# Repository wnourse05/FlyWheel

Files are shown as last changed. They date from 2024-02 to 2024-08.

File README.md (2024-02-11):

# FlyWheel

Hardware and Software for FlyWheel, a mobile robot for testing models of Fruit Fly Vision.

## Project Organization
- /hardware: Bill of materials and stl files for manufacturing FlyWheel
- /sns_flywheel: ROS package for controlling FlyWheel
- camera_overrides.isp: Preference file for proper color calibration of the cameras, from https://jonathantse.medium.com/fix-pink-tint-on-jetson-nano-wide-angle-camera-a8ce5fbd797f. See Installation for details
- robot_driver.ino: Arduino sketch to control the motors as a ros node.

## Installation

### Hardware Configuration
Please refer to the hardware directory for more information.

### Software Configuration
- Flash the sd card and set up the Jetson following the directions at: https://developer.nvidia.com/embedded/learn/get-started-jetson-orin-nano-devkit#intro . This project is built using Jetpack 5.1.2, available at: https://developer.nvidia.com/embedded/jetpack-sdk-512
- Install ROS-Noetic following the instructions at: http://wiki.ros.org/noetic
- Set up a catkin workspace following the instructions at: http://wiki.ros.org/ROS/Tutorials/InstallingandConfiguringROSEnvironment
- Clone this repository into ~/catkin_ws/src
- Install the joy package using "sudo apt-get install ros-noetic-joy"
- Install pip: sudo apt install python3-pip
- Install libopenblas: sudo apt-get install libopenblas-dev
- Upgrade numpy: pip install --upgrade numpy
- Export the NVIDIA Jetson torch url using: export TORCH_INSTALL=https://developer.download.nvidia.cn/compute/redist/jp/v511/pytorch/torch-2.0.0+nv23.05-cp38-cp38-linux_aarch64.whl
- Install torch: pip install --no-cache $TORCH_INSTALL 
- Correct the camera color profiles using camera_overrides.isp, following the directions at https://jonathantse.medium.com/fix-pink-tint-on-jetson-nano-wide-angle-camera-a8ce5fbd797f

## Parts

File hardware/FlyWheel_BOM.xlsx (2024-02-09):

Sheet: Overall BOM
Name | Description | Unit Cost | Quantity | Extended Cost | Source
Robot Base
M2 Male to Male Nylon Hex Standoff Plastic Thread Motherboard Spacer Prototyping Accessories for PCB, Quadcopter Drone, Computer & Circuit Board Assortment Kit Black | Standoffs | $14.88 | 1 | $14.88 | https://www.amazon.com/gp/product/B07D78PFQL/ref=ppx_yo_dt_b_asin_title_o05_s00?ie=UTF8&psc=1
TB3 Wheel Tire Set-ISW-01 (2ea) | Dynamixel Wheels | $9.40 | 1 | $9.40 | https://www.robotis.us/tb3-wheel-tire-set-isw-01-2ea/
DYNAMIXEL XL430-W250-T | Motor | $49.90 | 2 | $99.80 | https://www.robotis.us/dynamixel-xl430-w250-t/
Cable Zip Ties,400 Pack Black Assorted Sizes 12+8+6+4 Inch,Multi-Purpose Self-Locking Nylon Cable Cord Management ,Plastic Wire Ties for Home,Office,Garden,Workshop. By HAVE ME TD | Zip Ties | $5.99 | 1 | $5.99 | https://www.amazon.com/HAVE-ME-TD-Cable-Ties/dp/B08TVLYB3Q
OpenRB-150 | Serial controller | $24.90 | 1 | $24.90 | https://www.robotis.us/openrb-150/
Robot Cable-3P 100mm 10pcs | Cables | $14.20 | 1 | $14.20 | https://www.robotis.us/robot-cable-3p-100mm-10pcs/
FP04-F18 2pcs | Dynamixel Tires | $3.80 | 1 | $3.80 | https://www.robotis.us/fp04-f18-2pcs/
Ball Caster - 3/4" Metal Ball | Roller ball | $4.95 | 1 | $4.95 | https://www.adafruit.com/product/1200
ELEGOO PLA Filament 1.75mm Black | Filament | $13.99 | 1 | $13.99 | https://www.amazon.com/gp/product/B0BM739JRF/ref=ppx_yo_dt_b_asin_title_o05_s00?ie=UTF8&psc=1
JXMOX Short USB C to USB C Cable 60W, (2 Pack 1ft) Type C Fast Charging Cord Charger Compatible with iPhone 15 Plus/15 Pro Max, MacBook Pro, iPad Pro Air 4, Samsung Galaxy S23+ S22 S21 Ultra (Grey) | USB C to C Cable | $5.68 | 1 | $5.68 | https://www.amazon.com/gp/product/B07TVMBZ75/ref=ppx_yo_dt_b_asin_title_o05_s00?ie=UTF8&th=1
Talentcell Lithium ion Battery Pack NB7102, Rechargeable 17500mAh 64.75Wh Li-ion Power Bank with DC 24/19/5V and USB-C 5/9/12/15/20V Output for Laptop, Notebook, Smartphone, Camera and More | Battery | $62.99 | 1 | $62.99 | https://www.amazon.com/gp/product/B07RDFM55J/ref=ppx_od_dt_b_asin_title_s00?ie=UTF8&psc=1
3FT 12V DC Power Cable | 5.5mm x 2.1mm Male Plug to Bare Wire Open End | 16AWG 24V DC Power Supply Repair Cable | for CCTV Security Camera LED Strip Light | Motor power cable | $5.99 | 1 | $5.99 | https://www.amazon.com/gp/product/B09SQCY6BC/ref=ppx_od_dt_b_asin_title_s00?ie=UTF8&psc=1
Valefod 3 Pack LM2596 DC to DC Voltage Regulator | 4-40V to 1.5-35V Buck Converter | with LED Display | Buck Regulator | $13.99 | 1 | $13.99 | https://www.amazon.com/gp/product/B07WQJ2GD6/ref=ppx_od_dt_b_asin_title_s02?ie=UTF8&psc=1
Arduino MKR IMU Shield [ASX00002] Original Arduino Board Made in Italy Based on BNO055 Absolute Orientation Sensor 14-bit Accelerometer a triaxial 16-bit Gyroscope triaxial geomagnetic Sensor | IMU | $29.99 | 1 | $29.99 | https://www.amazon.com/gp/product/B09RPBKSZT/ref=ppx_od_dt_b_asin_title_s03?ie=UTF8&psc=1
 |  |  | Subtotal: | $310.55
Robot Computation
Yahboom 8MP IMX219 CSI Camera Compatible with NVIDIA Jetson Nano Developer Kit 3280×2464 Vision IR 77°/120°/160° Ultra Wide Angle Camera Module (IMX219 160°Camera+15/22pin) | 160 degree CSI camera | $28.99 | 2 | $57.98 | https://www.amazon.com/gp/product/B0C584LT6F/ref=ox_sc_act_title_1?smid=A1N1A77RUX51FT&psc=1
Arcade Button with LED - 30mm Translucent Clear | Power button | $2.50 | 1 | $2.50 | https://www.adafruit.com/product/3491
GL.iNet GL-SFT1200 (Opal) Secure Travel WiFi Router – AC1200 Dual Band Gigabit Ethernet Wireless Internet Router | IPv6 | USB 2.0 | MU-MIMO | DDR3 |128MB Ram | Repeater Bridge | Access Point Mode | Router | $39.90 | 1 | $39.90 | https://www.amazon.com/GL-iNet-GL-SFT1200-Secure-Travel-Router/dp/B09N72FMH5
Cat 8 Ethernet Cable, 1.5Ft 3Ft 6Ft 10Ft 15Ft 20Ft 30Ft 40Ft 50Ft 60Ft 100Ft Heavy Duty High Speed Internet Network Cable, Professional LAN Cable Shielded in Wall, Indoor&Outdoor | Ethernet | $2.99 | 1 | $2.99 | https://www.amazon.com/dp/B08PL53JG3/ref=twister_B08PP81V1L?_encoding=UTF8&psc=1
NVIDIA Jetson Orin Nano Developer Kit | Computer | $499.00 | 1 | $499.00 | https://www.amazon.com/NVIDIA-Jetson-Orin-Nano-Developer/dp/B0BZJTQ5YP
ELEGOO 120pcs Multicolored Dupont Wire 40pin Male to Female, 40pin Male to Male, 40pin Female to Female Breadboard Jumper Ribbon Cables Kit Compatible with Arduino Projects | Button wires | $6.98 | 1 | $6.98 | https://www.amazon.com/Elegoo-EL-CP-004-Multicolored-Breadboard-arduino/dp/B01EV70C78
GameSir T3s Wireless Gaming Controller for Switch, PC Windows, Bluetooth Controller with Turbo Function, Dual Shock, 25 Hours of Playing Time for Android/iPhone/Android TV Box/Tablet (Black) | Controller | $30.99 | 1 | $30.99 | https://www.amazon.com/gp/product/B09ZQWR5RD/ref=ppx_od_dt_b_asin_title_s01?ie=UTF8&th=1
SanDisk 128GB Extreme microSDXC UHS-I Memory Card with Adapter | Up to 190MB/s | C10 | U3 | V30 | 4K | 5K | A2 | Micro SD Card | SDSQXAA-128G-GN6MA | uSD card | $19.99 | 1 | $19.99 | https://www.amazon.com/gp/product/B09X7BK27V/ref=ppx_od_dt_b_asin_title_s02?ie=UTF8&th=1
Arcade Button Quick-Connect Wire Pairs - 0.11" (10 pack) | Button wires | $4.95 | 1 | $4.95 | https://www.adafruit.com/product/1152
Jumper Shunt with Handle (0.1" / 2.54mm) – 10 Pack | Shunt | $0.95 | 1 | $0.95 | https://www.adafruit.com/product/3525
 |  |  | Subtotal: | $666.23
 |  |  | Total: | $976.78

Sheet: Adafruit
Name | Description | Unit Cost | Quantity | Extended Cost | Source
Ball Caster - 3/4" Metal Ball | Roller ball | $4.95 | 1 | $4.95 | https://www.adafruit.com/product/1200
Adafruit TDK InvenSense ICM-20948 9-DoF IMU (MPU-9250 Upgrade) - STEMMA QT / Qwiic | IMU | $14.95 | 1 | $14.95 | https://www.adafruit.com/product/4554
STEMMA QT / Qwiic JST SH 4-pin Cable with Premium Female Sockets - 150mm Long | IMU cable | $0.95 | 1 | $0.95 | https://www.adafruit.com/product/4397
Arcade Button with LED - 30mm Translucent Clear | Power button | $2.50 | 1 | $2.50 | https://www.adafruit.com/product/3491
 |  |  | Total: | $23.35

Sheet: Robotis
Name | Description | Unit Cost | Quantity | Extended Cost | Source
FP04-F17 2pcs | Dynamixel Wheels | $2.50 | 1 | $2.50 | https://www.robotis.us/fp04-f17-2pcs/ | Robot base
DYNAMIXEL AX-12W | Motor | $49.90 | 2 | $99.80 | https://www.robotis.us/dynamixel-ax-12w/
U2D2 | Serial controller | $32.10 | 1 | $32.10 | https://www.robotis.us/u2d2/
Robot Cable-3P 100mm 10pcs | Cables | $14.20 | 1 | $14.20 | https://www.robotis.us/robot-cable-3p-100mm-10pcs/
FP04-F18 2pcs | Dynamixel Tires | $3.80 | 1 | $3.80 | https://www.robotis.us/fp04-f18-2pcs/
Robot Cable-X3P 180mm (Convertible) (10pcs) | Molex to JST Cable | $15.50 | 1 | $15.50 | https://www.robotis.us/robot-cable-x3p-180mm-convertible-10pcs/
U2D2 Power Hub Board Set | Power hub | $19.00 | 1 | $19.00 | https://www.robotis.us/u2d2-power-hub-board-set/
 |  |  | Total: | $186.90

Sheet: Amazon
Name | Description | Unit Cost | Quantity | Extended Cost | Source
M2 Male to Male Nylon Hex Standoff Plastic Thread Motherboard Spacer Prototyping Accessories for PCB, Quadcopter Drone, Computer & Circuit Board Assortment Kit Black | Standoffs | $8.99 | 1 | $8.99 | https://www.amazon.com/Motherboard-Prototyping-Accessories-Quadcopter-Assortment/dp/B07DBY4GQ8 | Robot Base
SUNGUY USB C Android Auto Cable 1FT, USB C to USB 3.1 USB 3.2 Gen2 10Gbps USB A to C Data Fast Charging Cable Compatible with Samsung Galaxy S21 S20 S10 S10E Note 20, USB C External C SSD, Pixel | USB A to C Cable | $7.99 | 1 | $7.99 | https://www.amazon.com/SUNGUY-Android-Charging-Compatible-External/dp/B0B28ZCV2Y | Robot Base
Talentcell Rechargeable 12V 6000mAh/5V 12000mAh DC Output Lithium ion Battery Pack for LED Strip and CCTV Camera, Portable Li-ion Power Bank with Charger, Black | Battery | $39.99 | 1 | $39.99 | https://www.amazon.com/TalentCell-Rechargeable-12000mAh-Multi-led-indicator/dp/B00ME3ZH7C | Robot Base
AILTECK 12V 5.5mm x 2.1mm Female to Female DC Power Connector Adapter, Male to Male Power Plug Jack Barrel for Led Strip Light CCTV Security Camera | Barrel adapter | $5.49 | 1 | $5.49 | https://www.amazon.com/AILTECK-Connector-Adapter-Female-Security/dp/B08V21NX8L | Robot Base
Yahboom 8MP IMX219 CSI Camera Compatible with NVIDIA Jetson Nano Developer Kit 3280×2464 Vision IR 77°/120°/160° Ultra Wide Angle Camera Module (IMX219 160°Camera+15/22pin) | 160 degree CSI camera | $28.99 | 2 | $57.98 | https://www.amazon.com/gp/product/B0C584LT6F/ref=ox_sc_act_title_1?smid=A1N1A77RUX51FT&psc=1 | Robot Compute
GL.iNet GL-SFT1200 (Opal) Secure Travel WiFi Router – AC1200 Dual Band Gigabit Ethernet Wireless Internet Router | IPv6 | USB 2.0 | MU-MIMO | DDR3 |128MB Ram | Repeater Bridge | Access Point Mode | Router | $39.90 | 1 | $39.90 | https://www.amazon.com/GL-iNet-GL-SFT1200-Secure-Travel-Router/dp/B09N72FMH5 | Robot Compute
Cat 8 Ethernet Cable, 1.5Ft 3Ft 6Ft 10Ft 15Ft 20Ft 30Ft 40Ft 50Ft 60Ft 100Ft Heavy Duty High Speed Internet Network Cable, Professional LAN Cable Shielded in Wall, Indoor&Outdoor | Ethernet | $2.99 | 1 | $2.99 | https://www.amazon.com/dp/B08PL53JG3/ref=twister_B08PP81V1L?_encoding=UTF8&psc=1 | Robot Compute
ELEGOO 120pcs Multicolored Dupont Wire 40pin Male to Female, 40pin Male to Male, 40pin Female to Female Breadboard Jumper Ribbon Cables Kit Compatible with Arduino Projects | Button wires | $6.98 | 1 | $6.98 | https://www.amazon.com/Elegoo-EL-CP-004-Multicolored-Breadboard-arduino/dp/B01EV70C78 | Robot Compute
 |  |  | Total: | $170.31

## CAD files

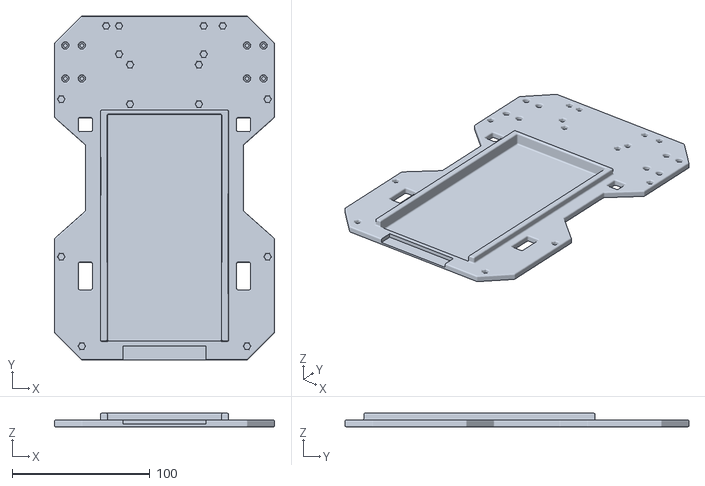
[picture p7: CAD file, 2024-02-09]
hardware/stl/base_plate_fillet.stl
160.0 x 250.0 x 10.0

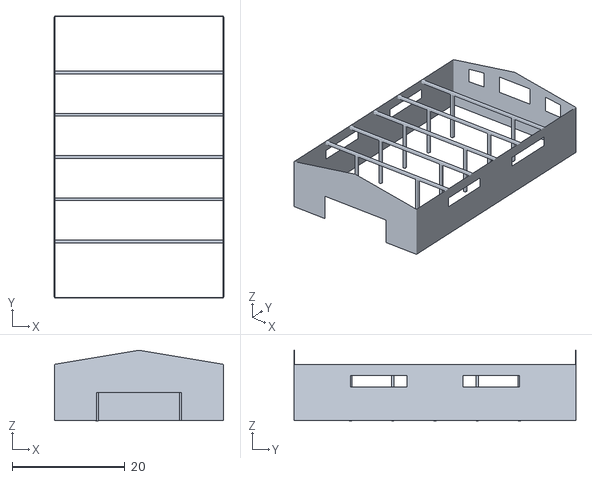
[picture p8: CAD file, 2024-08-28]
sns_flywheel/meshes/warehouse_colision.stl
30.0 x 50.0 x 12.5

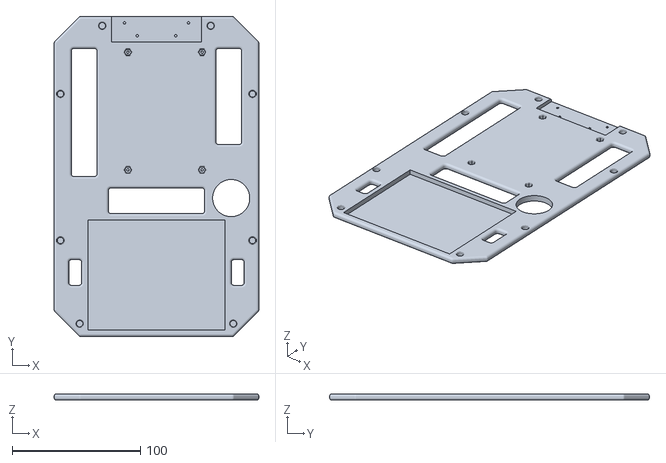
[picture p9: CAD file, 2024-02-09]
hardware/stl/top_plate_no_hole_small_slot.stl
160.0 x 250.0 x 5.00

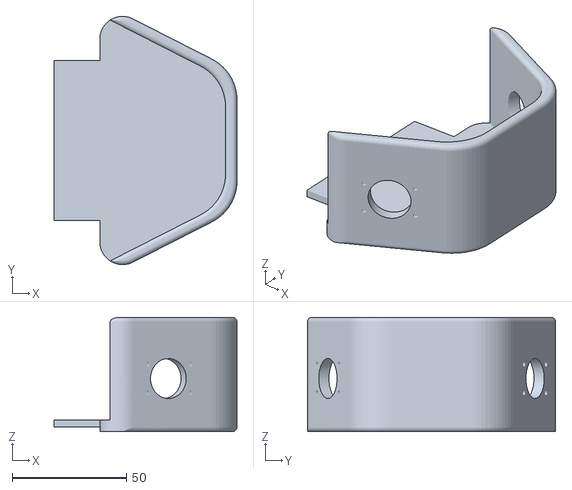
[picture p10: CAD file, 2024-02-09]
hardware/stl/head.stl
80.0 x 108.5 x 50.0

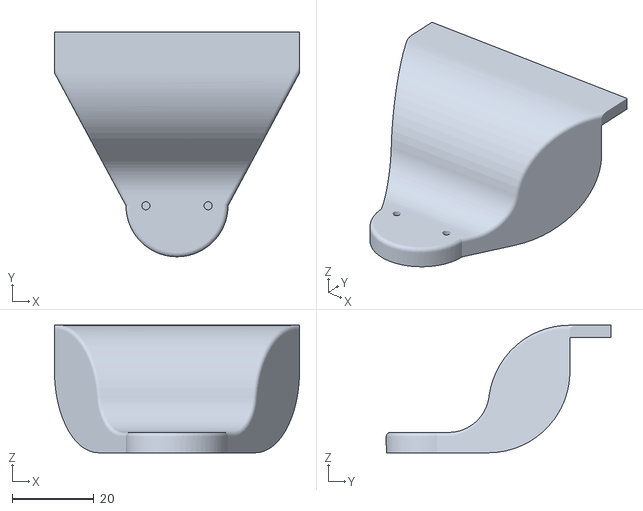
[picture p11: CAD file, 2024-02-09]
hardware/stl/ball_mount.stl
60.0 x 55.0 x 31.2

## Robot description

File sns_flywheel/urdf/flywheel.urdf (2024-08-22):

<?xml version="1.0"?>
<robot name="flywheel">
  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

  <link name="base_link">
  </link>

  <joint name="chassis_joint" type="fixed">
    <parent link="base_link"/>
    <child link="chassis"/>
    <origin xyz="0 0 0"/>
  </joint>
  <link name="chassis">
    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
    <inertial>
      <mass value="1.414"/>
      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
      <origin rpy="0 0 0" xyz="-0.107705 0 .0235"/>
    </inertial>
  </link>
  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

  <joint name="camera_left_joint" type="fixed">
    <parent link="chassis"/>
    <child link="camera_left"/>
    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
    <origin rpy="0 0 1.047151" xyz="0.0502 0.049522 0.0795"/>
  </joint>
  <link name="camera_left">
    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
    <inertial>
      <mass value="2.8498940e-02" />
      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
    </inertial>
  </link>
  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
  <joint name="camera_left_optical_joint" type="fixed">
    <origin xyz="0 0 0" rpy="-1.57075 0 -1.57075" />
    <parent link="camera_left" />
    <child link="camera_left_optical" />
  </joint>
  <link name="camera_left_optical"></link>

  <joint name="camera_right_joint" type="fixed">
    <parent link="chassis"/>
    <child link="camera_right"/>
    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
    <origin rpy="0 0 -1.047151" xyz="0.0502 -0.049522 0.0795"/>
  </joint>
  <link name="camera_right">
    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
    <inertial>
      <mass value="2.8498940e-02" />
      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
    </inertial>
  </link>
  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
  <joint name="camera_right_optical_joint" type="fixed">
    <origin xyz="0 0 0" rpy="-1.57075 0 -1.57075" />
    <parent link="camera_right" />
    <child link="camera_right_optical" />
  </joint>
  <link name="camera_right_optical"></link>

  <link name="caster">
    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
    <inertial>
      <mass value="0.00001"/>
      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
      <origin rpy="1.57075 0 0" xyz="0 0.008692 0"/>
    </inertial>
  </link>
  <joint name="caster_joint" type="fixed">
    <parent link="chassis"/>
    <child link="caster"/>
    <origin xyz="0 0 0"/>
  </joint>
  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

  <link name="wheel_left">
    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
    <inertial>
      <mass value="2.8498940e-02" />
      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
      <origin rpy="1.57075 0 0" xyz="0 0.008692 0"/>
    </inertial>
  </link>
  <joint name="base_to_wheel_left" type="continuous">
    <parent link="chassis"/>
    <child link="wheel_left"/>
    <axis xyz="0 1 0"/>
    <origin xyz="0 0.08 0"/>
  </joint>
  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

  <link name="wheel_right">
    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
    <inertial>
      <mass value="2.8498940e-02" />
      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
      <origin rpy="1.57075 0 0" xyz="0 -0.008692 0"/>
    </inertial>
  </link>
  <joint name="base_to_wheel_right" type="continuous">
    <parent link="chassis"/>
    <child link="wheel_right"/>
    <axis xyz="0 1 0"/>
    <origin xyz="0 -0.08 0"/>
  </joint>
  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
</robot>

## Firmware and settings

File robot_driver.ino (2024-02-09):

/*
 * rosserial Publisher Example
 * Prints "hello world!"
 */

// Use the following line if you have a Leonardo or MKR1000
#define USE_USBCON

#include <ros.h>
#include <std_msgs/String.h>
#include <geometry_msgs/Twist.h>
#include <Dynamixel2Arduino.h>

//#include <MKRIMU.h>
#include <Wire.h>
#include <Adafruit_Sensor.h>
#include <Adafruit_BNO055.h>
#include <utility/imumaths.h>

#define DXL_SERIAL Serial1
#define DEBUG_SERIAL Serial
const int DXL_DIR_PIN = -1;

const uint8_t LEFT = 1; //left motor
const uint8_t RIGHT = 0;  //right motor
const float DXL_PROTOCOL_VERSION = 2.0;

const int8_t DIR_LEFT = 1;
const int8_t DIR_RIGHT = -1;
const float WHEEL_RAD = 0.033;  //meters
const float WHEEL_BASE = 0.184; // meters

uint8_t ITER = 0;

float vel = 0.0;
float newvel = 0.0;
float w = 0.0;
float rpm_left = 0.0;
float rpm_right = 0.0;
float w_left = 0.0;
float w_right = 0.0;

float w_x = 0.0;
float w_y = 0.0;
float w_z = 0.0;

bool read_IMU = true;
bool drive_motor = true;

unsigned long timer = millis();

/* Set the delay between fresh samples */
#define BNO055_SAMPLERATE_DELAY_MS (100)

// Check I2C device address and correct line below (by default address is 0x29 or 0x28)
//                                   id, address
Adafruit_BNO055 bno = Adafruit_BNO055(-1, 0x28, &Wire);

void cmdVelCallback(const geometry_msgs::Twist& twist){
  vel = twist.linear.x;
  w = twist.angular.z;
}

ros::NodeHandle nh;

geometry_msgs::Twist cmd_vel;
ros::Subscriber<geometry_msgs::Twist> sub("cmd_vel", &cmdVelCallback);

geometry_msgs::Twist imu_msg;
ros::Publisher imu_reading("imu", &imu_msg);

Dynamixel2Arduino dxl(DXL_SERIAL, DXL_DIR_PIN);
using namespace ControlTableItem;

int set_mode_velocity(int DXL_ID) {
  dxl.torqueOff(DXL_ID);
  dxl.setOperatingMode(DXL_ID, OP_VELOCITY);
  dxl.torqueOn(DXL_ID);
}

int spin_motor(int DXL_ID, float RPM, int DIR) {
  if(RPM==0){
    dxl.ledOff(DXL_ID);
  }else{
    dxl.ledOn(DXL_ID);
  }
  dxl.setGoalVelocity(DXL_ID, RPM*DIR, UNIT_RPM);
}


float convert_w_to_rpm(float w){
  return 60*w/(2*PI);
}

void setup()
{
  DEBUG_SERIAL.begin(9600);
  
  nh.getHardware()->setBaud(9600);
  nh.initNode();
  if (read_IMU){
    nh.advertise(imu_reading);
  }
  if (drive_motor){
    nh.subscribe(sub);

    // Set Dynamixel Baudrate and protocol version, must match current configuration of motors
    dxl.begin(57600);
    dxl.setPortProtocolVersion(DXL_PROTOCOL_VERSION);

    // Configure motors for velocity mode
    set_mode_velocity(LEFT);
    set_mode_velocity(RIGHT);
  }
  while(!nh.connected()){
    nh.spinOnce();
  }
  nh.loginfo("Connected to OpenRB-150");

  if (read_IMU){
    while (!bno.begin()){
      nh.loginfo("Failure connecting to IMU, trying again");
      nh.spinOnce();
    }
    nh.loginfo("IMU Connection Established");
    bno.setExtCrystalUse(true);
  }
}

void loop()
{
  while(!nh.connected()){
    spin_motor(LEFT, 0, DIR_LEFT);
    spin_motor(RIGHT, 0, DIR_RIGHT);
    nh.spinOnce();
  }
  if (drive_motor){
    w_left = (vel-(w*WHEEL_BASE)/2)/WHEEL_RAD;
    w_right = (vel+(w*WHEEL_BASE)/2)/WHEEL_RAD;
    rpm_left = convert_w_to_rpm(w_left);
    rpm_right = convert_w_to_rpm(w_right);
    spin_motor(LEFT, rpm_left, DIR_LEFT);
    spin_motor(RIGHT, rpm_right, DIR_RIGHT);
  }
  if (read_IMU){
    imu::Vector<3> gyro = bno.getVector(Adafruit_BNO055::VECTOR_GYROSCOPE);
    imu_msg.angular.x = gyro.x();
    imu_msg.angular.y = gyro.y();
    imu_msg.angular.z = gyro.z();

    imu_reading.publish( &imu_msg);
  }
  
  nh.spinOnce();
  //delay(15);
}

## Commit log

2024-02-09 stl files
    [ball_mount.stl, base_plate_fillet.stl, head.stl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]
2024-02-09 Added BOM
    [FlyWheel_BOM.xlsx]
2024-08-22 Run experiment
    [edifice.sdf, flywheel.urdf, flywheel_office.sdf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]
2024-08-28 Expanded spawn radius
    [flywheel_office.sdf, warehouse.sdf, warehouse_colision.stl]
2024-08-29 Added bookstore
    [house.sdf, model.sdf]
